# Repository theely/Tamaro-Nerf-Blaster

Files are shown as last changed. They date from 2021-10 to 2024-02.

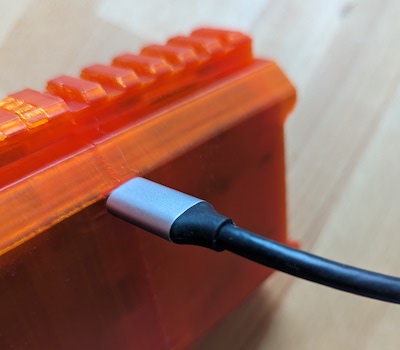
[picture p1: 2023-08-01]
docs/assets/img/tamaro-usbc-connected.jpg

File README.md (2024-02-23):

# An open-source 3D printable Nerf Rival compatible Blaster

PXL_20230726_122825097 (2)

## Mounting Instructions
Full assembly mounting instructions:
https://medium.com/@EliaPalme/tamaro-nerf-blaster-75f032bfdf08

## Part Sourcing
For convenience we offer pre-sourced hardware and electronics kit:
https://www.etsy.com/shop/TamaroBlaster

## Tamaro Blaster Configurator
The configurator allows you to fine-tune the parameters of your blaster. 
https://theely.github.io/Tamaro-Nerf-Blaster/

## Design Principles

The Tamaro blaster is inspired by the FDL3 and the OOD Jupiter blasters.
It has been designed with the following principles in mind:

### Simplicity and Elegance
Tamaro design focuses on minimalism and aesthetics, increases reliability and does not compromise on functionality.

### Small footprint
Tamaro total weight is 500g and dimensions are 245mm*158mm*48mm.

### Easy to print
Tamaro is made of 15 3D printed pieces with limited support required.

### Easy to source hardware
Tamaro only requires few M3 screws. The electronics is broadly available.

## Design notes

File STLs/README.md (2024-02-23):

# Printing Instructions

**Important: Don't change the parts orientation.**    
Each STL part has already been placed with the best possible orientation to reduce need for support and to improve print quality.

## Handles
- Support: Yes (slicer default works fine)
- Bridging: Yes (reduces need for support)
- Infil: 15%-20%
- Top solid layers: 4+

## Trigger
- Support: No
- Bridging: No
- Infil: 15%

## Magwell
- STL files: v1 for legacy magazines, v2 for the latest Nerf version.
- Support: Yes (custom)  
  Only the very bottom part requires support (see screenshot).
- Bridging: Yes
- Infil: 15%
 
Slicing Example

## Barrel
- Support: No
- Bridging: No
- Infil: 15%

## Motor Plates
- Support: No
- Bridging: No
- Infil: 40%
- Top and Bottom solid layers: 5+

## Clamp Front
- Support: No
- Bridging: No
- Infil: 20%

## Clamp Back
- Support: Yes (custom)  
  No support needed in screw and nut holes (see screenshot).
- Bridging: Yes
- Infil: 20%

Slicing Example

## Shells
- Support: Yes (custom)
  Support for cureved and angled surfaces can be supressed. 
- Bridging: Yes
- Infil: 15%
- Brim: Optionally consider adding a custom brim (see screenshot, four 1 layer squares) to prevent warping.
  


## Battery Hatch
- Support: No
- Bridging: No
- Infil: 15%

## Pusher
- Support: Yes
- Bridging: Yes
- Top and Bottom solid layers: 5+
- Perimeters: 5+
- Infil: 50%

## Battery Holder (optional)
This piece is optional and only needed if you would like to power the bluster with 16650 Li-Ion batteries insted of a LiPo battery.
- Support: Yes
- Bridging: Yes
- Infil: 15%

# QA
Tracking quality assurance parts printing tests and potential improvments.

| Part | Date | Status| Notes|
|---|---|---|---|
|Handle L|14-07-2023|Not yet printed|  | 
|Handle R|14-07-2023|Not yet printed|  | 
|Shell Back|14-07-2023|Assembled no issues| Add custom brim | 
|Barrel|30-06-2023 |Assembled no issues| Fast printing helps with overhangs | 
|Magwell|30-06-2023|Assembled no issues| Not an issue but one wall is too narrow and might end up with a small hole | 
|Clamp Front|02-07-2023|Assembled no issues|  | 
|Clamp Back|02-07-2023|Assembled no issues|  | 
|Motor Plates|02-07-2023|Assembled no issues|  | 
|Trigger|02-07-2023|Assembled no issues|  | 
|Pusher|02-07-2023|Assembled no issues|  | 
|Shell Frot|05-07-2023|Assembled no issues|  |

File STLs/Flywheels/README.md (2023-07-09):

# Printing Instructions

**Important: Don't change the parts orientation.**    
Each STL part has already been placed with the best possible orientation to reduce need for support and to improve print quality.

## EMAX RS2205 Flywheel
- Support: No
- Bridging: No
- Seam position: Random
- Infil: Rectilinear (important!) 20%
- Top solid layers: 5+
- Perimeters: 5+

## T-Motor 2205 Flywheel
- Support: No
- Bridging: No
- Seam position: Random
- Infil: Rectilinear (important!) 20%
- Top solid layers: 5+
- Perimeters: 5+

# QA
Tracking quality assurance parts printing tests and potential improvments.

| Part | Date | Status| Notes|
|---|---|---|---|
|EMAX RS2205|09-07-2023 |Printing|  |

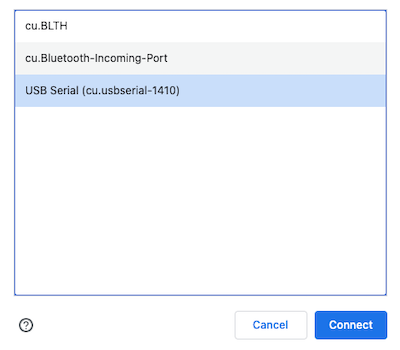
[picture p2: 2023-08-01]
docs/assets/img/select-device.jpg

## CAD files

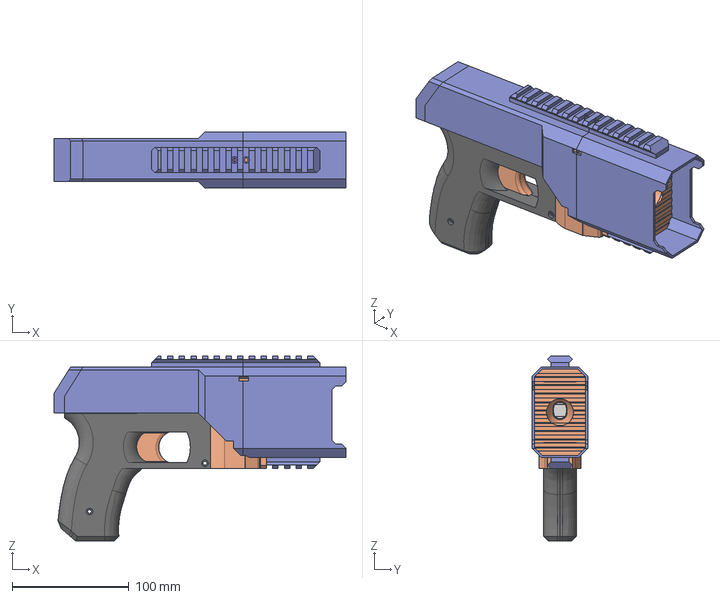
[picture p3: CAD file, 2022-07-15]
Hardware Designs Backup Exports/Blaster.stp
249.8 x 48.0 x 158.2 mm

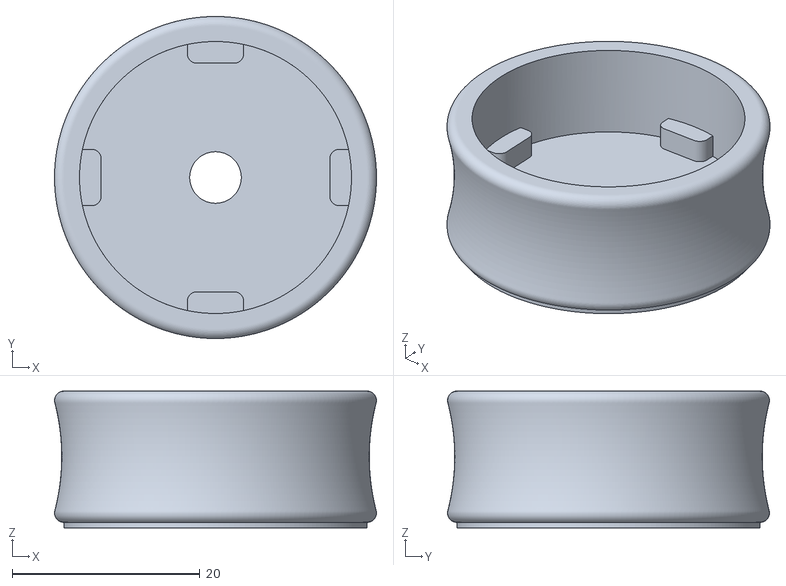
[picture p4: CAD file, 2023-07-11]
STLs/Flywheels/EMAX RS2205 (+0.5) Flywheel.stl
34.3 x 34.3 x 14.6

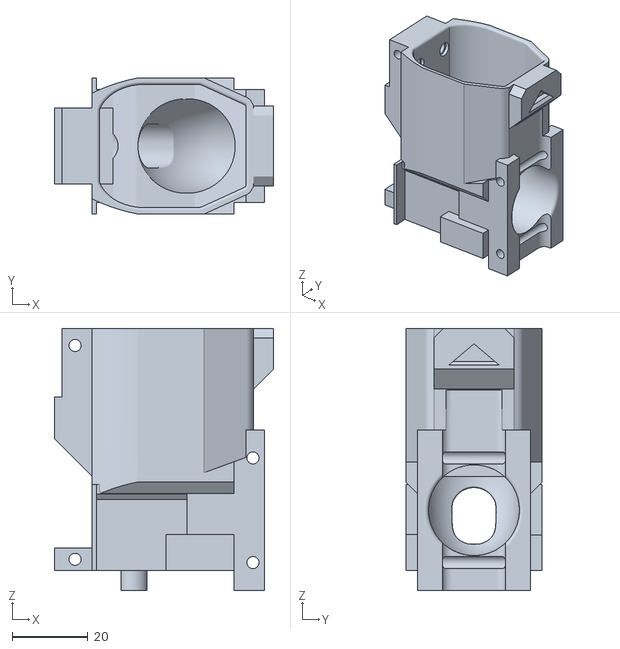
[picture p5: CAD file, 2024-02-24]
STLs/Magwell-v2.1.stl
58.1 x 36.0 x 69.4

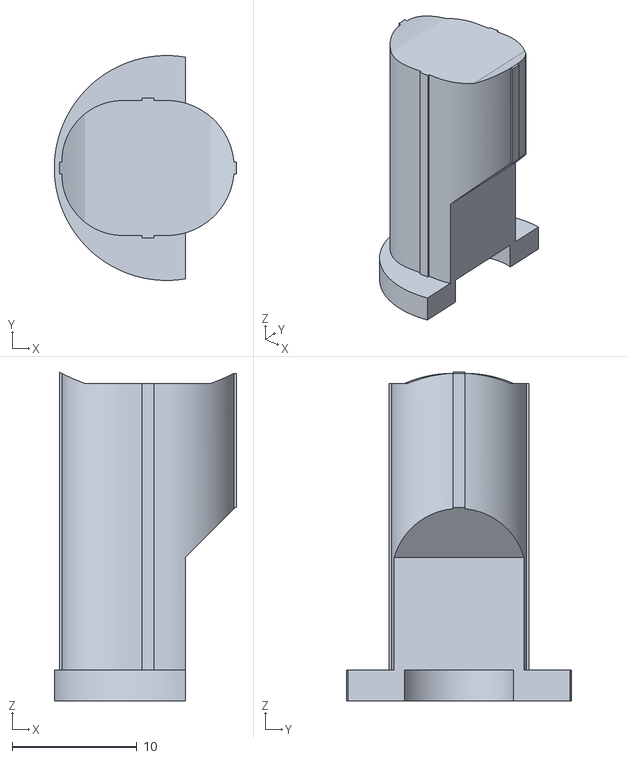
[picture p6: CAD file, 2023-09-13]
STLs/Pusher/Pusher.stl
14.6 x 18.0 x 26.3

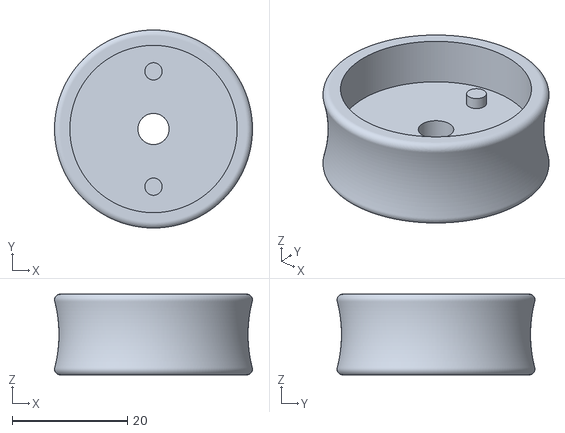
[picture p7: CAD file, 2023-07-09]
STLs/Flywheels/T-Motor 2205 (+0.4) Flywheel.stl
34.3 x 34.3 x 14.0

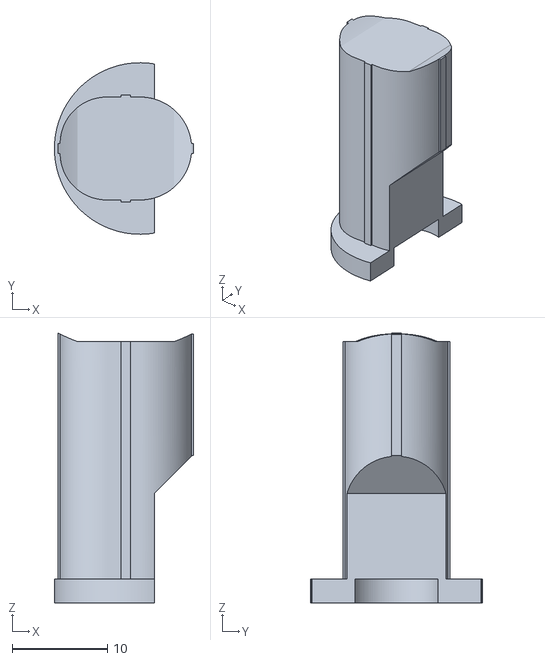
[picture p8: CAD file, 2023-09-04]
STLs/Pusher/Pusher (+2.0L).stl
14.6 x 18.0 x 28.3

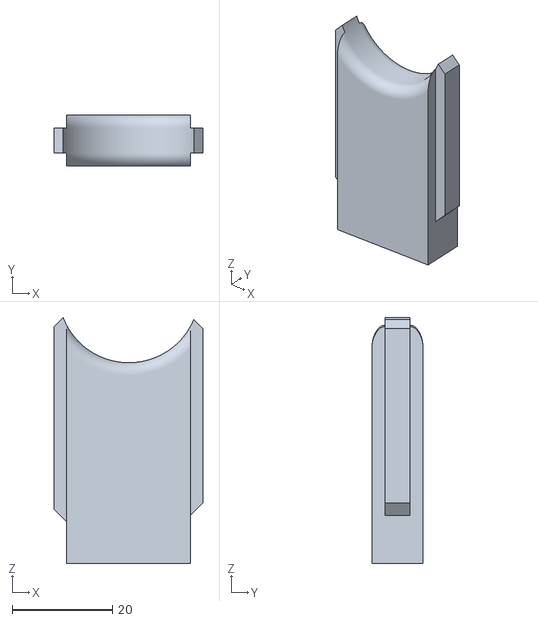
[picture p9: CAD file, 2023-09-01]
STLs/Trigger.stl
29.6 x 10.2 x 49.0

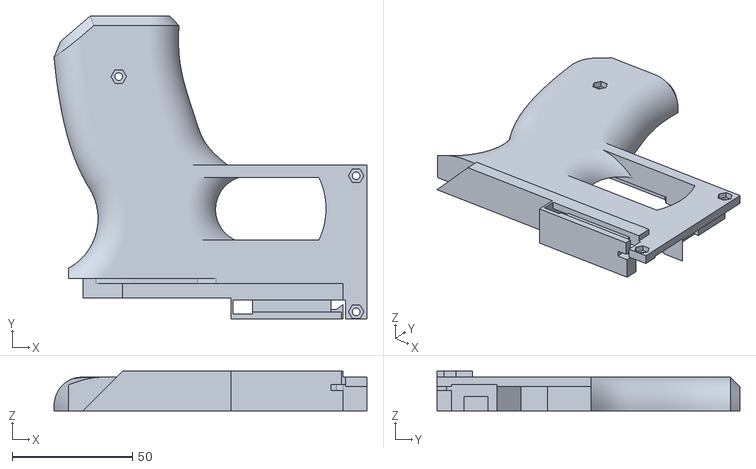
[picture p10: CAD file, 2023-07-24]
STLs/Handle L.stl
130.3 x 126.1 x 16.5

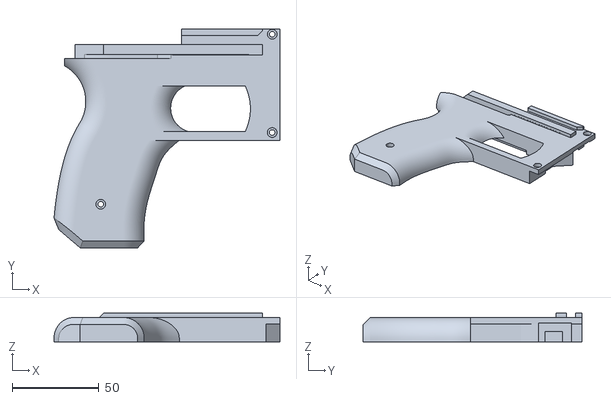
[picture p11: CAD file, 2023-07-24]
STLs/Handle R.stl
130.3 x 126.1 x 16.5

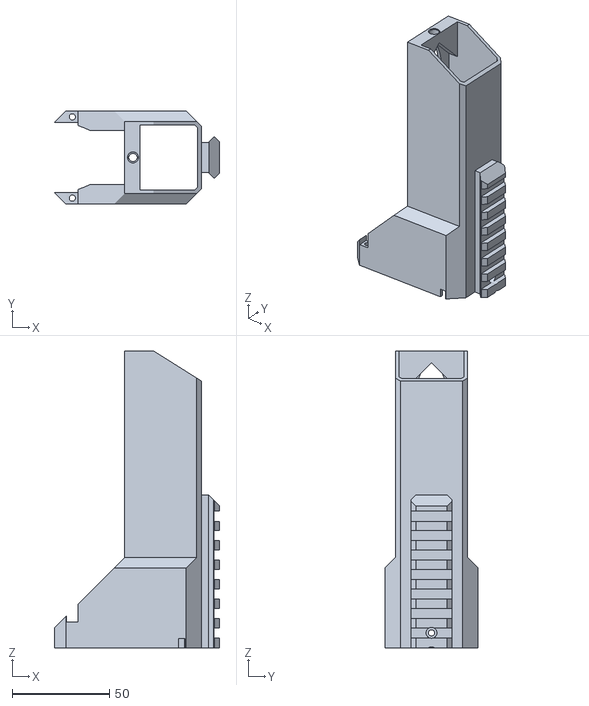
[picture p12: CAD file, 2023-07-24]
STLs/Shell Back.stl
85.0 x 48.0 x 152.8

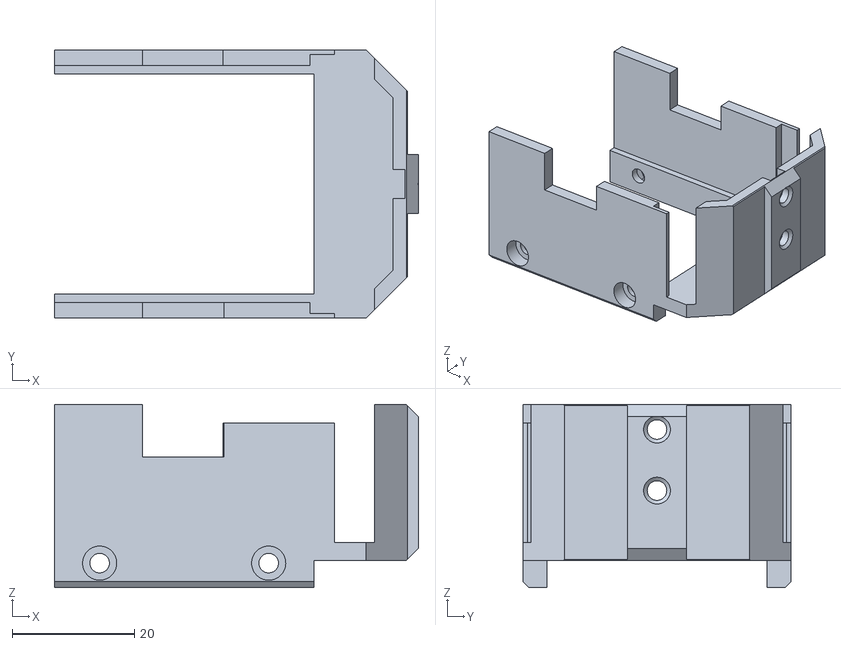
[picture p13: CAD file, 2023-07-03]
STLs/Clamp Back.stl
59.6 x 44.0 x 30.0

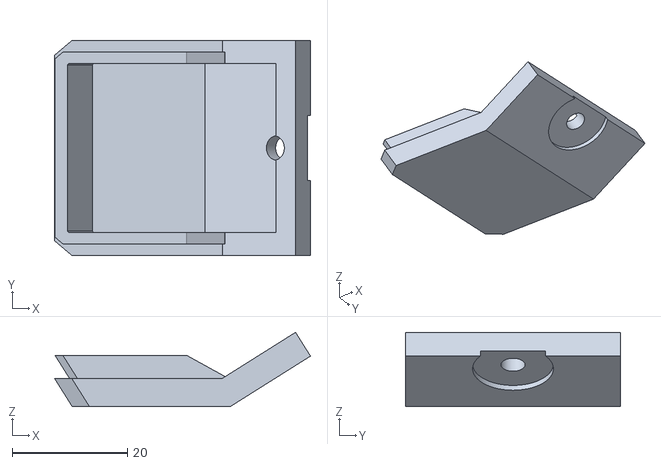
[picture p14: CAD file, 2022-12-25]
STLs/Battery Hatch.stl
44.3 x 37.2 x 12.9

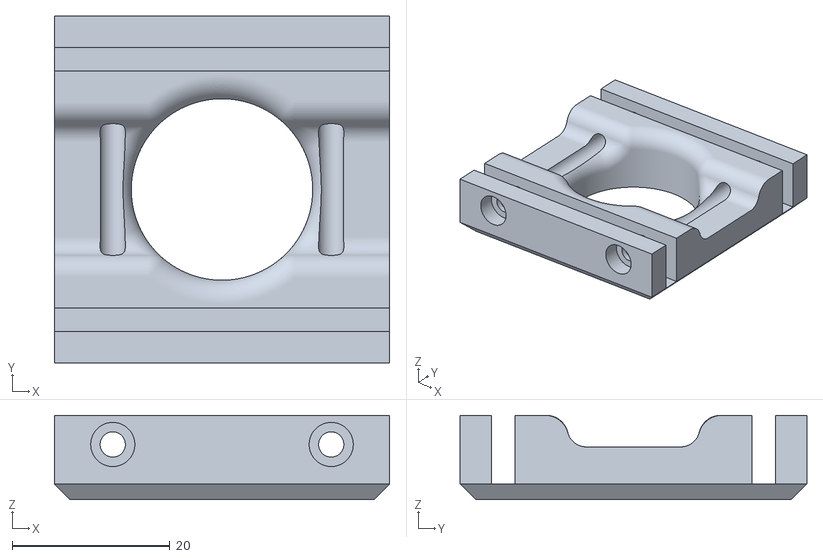
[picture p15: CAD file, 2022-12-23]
STLs/Clamp Front.stl
42.5 x 44.0 x 10.7

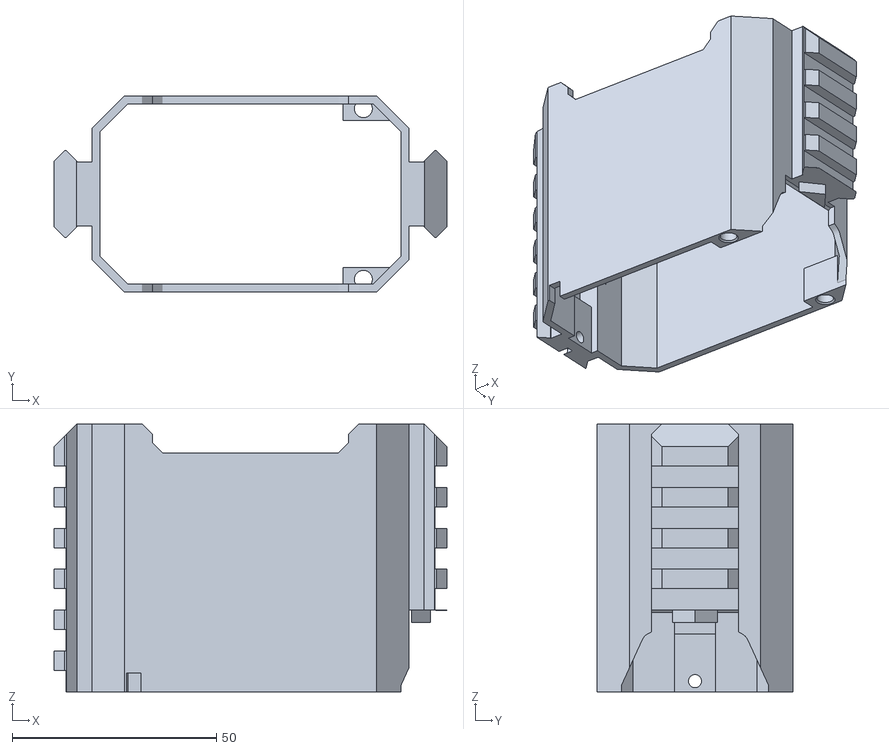
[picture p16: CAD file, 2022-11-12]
STLs/Shell Front.stl
96.2 x 48.0 x 65.5

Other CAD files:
STLs/Flywheels/EMAX RS2205 (+0.4) Flywheel.stl
STLs/Pusher/Pusher (+2.0L +0.2C).stl
STLs/Motor Plate.stl
STLs/Barrel.stl
Hardware Designs Backup Exports/Blaster+PCB.f3z
STLs/Magwell-v1.stl

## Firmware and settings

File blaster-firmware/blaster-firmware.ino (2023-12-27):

#include "DShot.h"
#include <EEPROM.h>
#include <ButtonDebounce.h>


#define SERIAL_SPEED 115200


//TODO implment BlHeli passthrough: https://github.com/BrushlessPower/BlHeli-Passthrough



int solenoid = 2;
int esc1Pin = 3;
//4 unused
//5 unused
int esc2Pin = 6;
int triggerPin = 7;
int revPin = 8;
//9 unused
//10 unused
// 11 unused
// 12 unused

int LED = 13;

//pin 15 used for analog input A1


String version = "0.1";


#define CONFIGURATION_VERSION  10

struct Confing {
  int  pusher_pull_time;     //time required for the pusher to move
  int  pusher_push_time;     //time required for the pusher to move
  int  esc_max_power;
  int  min_rampup_time;      //time required for the flywheel to get up to speed
  int  spin_differential;    //how much slower the bottom wheel should turn
  int  inactivity_time_out;  //After how much self shutdown
  int  warning_vbat;         //Vbat voltage to trigger warning
  int  critical_vbat;        //Vbat voltage to trigger shutdown
  int  vbat_scale;           //Used to calibrate vbat measurment
  int  config_version;      //IMPORTANT: increment config version for every change of this struct
};


Confing configuration = {
  110,         //pusher_pull_time -- min: 65 (tested)
  90,          //pusher_push_time -- min: 55 (tested)
  1500,        //esc_max_power
  140,         //min_rampup_time
  150,         //spin_differential
  30,          //inactivity_time_out
  10,          //warning_vbat
  9,           //critical_vbat
  12,          //vbat_scale
  CONFIGURATION_VERSION
};

struct ConfigParam {
  String  name;
  int     default_value;
  int     max_value;
  int     min_value;
  int*    value;
};

ConfigParam config_params[9] = {
  ConfigParam{"pusher_pull_time",110,500,10,&configuration.pusher_pull_time},
  ConfigParam{"pusher_push_time",90,500,10,&configuration.pusher_push_time},
  ConfigParam{"esc_max_power",1500,2047,200,&configuration.esc_max_power},
  ConfigParam{"min_rampup_time",140,500,0,&configuration.min_rampup_time},
  ConfigParam{"spin_differential",150,300,0,&configuration.spin_differential},
  ConfigParam{"inactivity_time_out",30,60,0,&configuration.inactivity_time_out},
  ConfigParam{"warning_vbat",10,14,0,&configuration.warning_vbat},
  ConfigParam{"critical_vbat",9,14,0,&configuration.critical_vbat},
  ConfigParam{"vbat_scale",12,100,1,&configuration.vbat_scale},
};



enum states {Idle, Rampup, Ready, Fire, Hold, Click, Command};
const char* statesNames[] = {"Idle", "Rampup", "Ready", "Fire", "Hold", "Click", "Command"};

enum fireRates {Single, Auto, Burst};

enum states state = Idle;
enum states previous_state = Idle;
enum fireRates fireRate = Single;

int burstCount = 0;

String serial_command;

DShot ESC1(DShot::Mode::DSHOT300INV);
DShot ESC2(DShot::Mode::DSHOT300INV);

ButtonDebounce revButton(revPin, 40);
ButtonDebounce triggerButton(triggerPin, 40);


#if defined(__AVR_ATmega328P__)
  int long_beep=130;
  int short_beep=110;
#endif
#if defined(ARDUINO_ARCH_MEGAAVR)
  int long_beep=260;
  int short_beep=240;
#endif

unsigned long timer_rampup = 0;
unsigned long vabt_warning_timer = millis();

unsigned  int click_count=0;
unsigned long click_timeout = 500;
unsigned long inter_click_timer = 0;
unsigned long inter_click_timeout = 1000;

void setup() {

  pinMode(solenoid, OUTPUT);
  digitalWrite(solenoid, LOW);
  pinMode(LED, OUTPUT);
  digitalWrite(LED, LOW);

  Serial.begin(SERIAL_SPEED,SERIAL_8N1);


  ESC1.attach(esc1Pin);
  ESC2.attach(esc2Pin);
  ESC1.setThrottle(0);
  ESC2.setThrottle(0);
  setESC1speed(0);
  setESC2speed(0);

  analogReference(DEFAULT);

  Confing configuration_check;
  EEPROM.get( 0, configuration_check );
  if(configuration_check.config_version !=  configuration.config_version){
     //Config structure has changed reset config.
     Serial.println("Config structure mismatch detected");
     EEPROM.put(0, configuration);
     Serial.println("Re-setted configuration");
  }else{
    EEPROM.get( 0, configuration);
  }


  //initialize LiPo voltage
  getAvgLiPoVoltage();
}

void loop() {


  controlESCs();

  if (Serial.available()) {
    serial_command = Serial.readStringUntil('\n');
    char* token = strtok(serial_command.c_str(), "= ,\r\n");

    bool set_value = false;
    String variable_name;
    String variable_value;
    while (token != NULL) {

      if(strcmp(token, "version") == 0){
          Serial.println("Tamaro Blaster");
          Serial.print("version:");
          Serial.println(version);
      }

      if(strcmp(token, "vbat") == 0){
          Serial.print("vbat=");
          Serial.println(getLiPoVoltage());
      }

      if(strcmp(token, "dump") == 0){
        dump();
      }

      if (set_value && variable_name != NULL && variable_value == NULL) {
        variable_value = token;
      }
      if (set_value && variable_name == NULL) {
        variable_name = token;
      }
      if (strcmp(token, "set") == 0) {
        set_value = true;
      }
      token = strtok(NULL, "= ,\r\n");
    }

    if (set_value && variable_name != NULL && variable_value != NULL) {
      setSerialParam(variable_name, variable_value.toInt());
      EEPROM.put(0, configuration);
    }



  }

  state = getState();


  if(configuration.warning_vbat> 0 && getAvgLiPoVoltage() < configuration.warning_vbat){
      if((millis() - vabt_warning_timer)  > 10000){
        beep beeps[2];
        beeps[0]= {1, short_beep};
        beeps[1]= {1, short_beep};
        ESC1.sequenceBeep(beeps,2);
        vabt_warning_timer = millis();
      }
  }
  if(configuration.critical_vbat > 0 && getAvgLiPoVoltage() < configuration.critical_vbat){
    //TOODO disable blaster and allert
  }



  if (state == Rampup || state == Ready || state == Fire ) {

    digitalWrite(LED, HIGH);

    setESC1speed(configuration.esc_max_power);
    setESC2speed(max(configuration.esc_max_power-configuration.spin_differential,48));

  } else {
    digitalWrite(LED, LOW );

    setESC1speed(0);
    setESC2speed(0);
  }

  if (state == Fire ) {

    digitalWrite(solenoid, HIGH);
    delay(configuration.pusher_pull_time);
    digitalWrite(solenoid, LOW);
    delay(configuration.pusher_push_time);
  }
  if (state == Command) {

    click_count=0;
    ESC1.setThrottle(0);
    ESC2.setThrottle(0);
    delay(300);

    if (fireRate == Single) {
      fireRate = Burst;
      //   short - 3
      beep beeps[4];
      beeps[0]= {4, long_beep};
      beeps[1]= {1, short_beep};
      beeps[2]= {1, short_beep};
      beeps[3]= {1, short_beep};
      ESC1.sequenceBeep(beeps,4);
    } else if (fireRate == Burst) {
      fireRate = Auto;
      beep beeps[4];
      beeps[0]= {4, long_beep};
      beeps[1]= {1, short_beep};
      beeps[2]= {2, short_beep};
      beeps[3]= {3, short_beep};
      ESC1.sequenceBeep(beeps,4);
    } else {
      fireRate = Single;
       //   short - short
      beep beeps[2];
      beeps[0]= {4, long_beep};
      beeps[1]= {1, short_beep};
      ESC1.sequenceBeep(beeps,2);
    }
    delay(300);
  }

  //keep this statement at end of the loop
  if (previous_state != state) {
    //Serial.println(statesNames[state]);
    previous_state = state;
  }

}

enum states getState() {


    revButton.update();
    triggerButton.update();

    int revValue = !revButton.state();
    int triggerValue = !triggerButton.state();




  switch (state) {


    case Idle:
      if (revValue == HIGH) {
        timer_rampup = millis();
        return Rampup;
      }
      if (click_count > 1) {
        return Command;
      }
      return Idle;
      break;


    case Rampup :
      if (revValue == HIGH && (millis() - timer_rampup) > configuration.min_rampup_time) {
        return Ready;
      }
      if (revValue == HIGH) {
        return Rampup;
      }
      if (revValue == LOW && (millis() - timer_rampup) < click_timeout) {
        if((millis() - inter_click_timer) > inter_click_timeout){
          click_count=1;
        }else{
          click_count++;
        }
        inter_click_timer=millis();
        return Idle;
      }
      break;

    case Ready :
      if (triggerValue == HIGH) {
        burstCount = 1;
        return Fire;
      }
      if (revValue == HIGH && triggerValue == LOW) {
        return Ready;
      }
      break;

    case Fire:
      if (fireRate == Auto && triggerValue == HIGH) {
        return Fire;
      }
      if (fireRate == Burst && triggerValue == HIGH && burstCount < 3) {
        burstCount++;
        return Fire;
      }
      if (triggerValue == LOW) {
        return Idle;
      }
      return Hold;

    case Hold:
      if (revValue == LOW) {
        return Idle;
      }
      return Hold;


    default : break;
  }

  return Idle;
}


int esc1ActualSpeed = 0;
int esc2ActualSpeed = 0;
int esc1TargetSpeed = 0;
int esc2TargetSpeed = 0;


long timer_break_esc1 = 0;
long timer_break_esc2 = 0;

void setESC1speed(int speed){
   esc1TargetSpeed = speed;
}

void setESC2speed(int speed){
    esc2TargetSpeed = speed;
}

void controlESCs(){


  //Gradual speed decrease is required to avoid voltage spikes that would accidentally trigger the solenoid

  if(esc1ActualSpeed<esc1TargetSpeed){
    esc1ActualSpeed = esc1TargetSpeed;
    ESC1.setThrottle(esc1ActualSpeed);
  }else if(esc1ActualSpeed>esc1TargetSpeed && (millis() - timer_break_esc1 > 20)){
      timer_break_esc1 = millis();
      esc1ActualSpeed-=150;
      if(esc1ActualSpeed < esc1TargetSpeed){
        esc1ActualSpeed = esc1TargetSpeed;
      }
      ESC1.setThrottle(esc1ActualSpeed);
  }

  if(esc2ActualSpeed<esc2TargetSpeed){
    esc2ActualSpeed = esc2TargetSpeed;
    ESC2.setThrottle(esc2ActualSpeed);
  }else if(esc2ActualSpeed>esc2TargetSpeed && (millis() - timer_break_esc2 > 20)){
    timer_break_esc2 = millis();
    esc2ActualSpeed-=150;
    if(esc2ActualSpeed < esc2TargetSpeed){
      esc2ActualSpeed = esc2TargetSpeed;
    }
    ESC2.setThrottle(esc2ActualSpeed);
  }



}


void setSerialParam(String param, int value){

  for(int i=0;i<sizeof config_params/sizeof(struct ConfigParam);i++){
    if(param == config_params[i].name){

      if(value < config_params[i].min_value){
        Serial.print("Minimum value for ");
        Serial.print(param);
        Serial.print(" is ");
        Serial.println(config_params[i].min_value);
        return;
      }
      if(value > config_params[i].max_value){
        Serial.print("Maximum value for ");
        Serial.print(param);
        Serial.print(" is ");
        Serial.println(config_params[i].max_value);
        return;
      }

      *config_params[i].value=value;
      EEPROM.put(0, configuration);

      Serial.print(param);
      Serial.print(" set to ");
      Serial.println(value);

      return;
    }
  }
}


void dump(){

  for(int i=0;i<sizeof config_params/sizeof(struct ConfigParam);i++){
     Serial.print(config_params[i].name);
     Serial.print("=");
     Serial.println(*config_params[i].value);
  }
}



float getLiPoVoltage(){

  //https://www.arduino.cc/reference/en/language/functions/analog-io/analogread/
  //https://skillbank.co.uk/arduino/measure.htm


  float value = analogRead(A1);
  float voltage = (value + 0.5) * 5.0 / 1023.0 *   ((float) configuration.vbat_scale); //adj_multiplier
  //Calibration formula: current_scale * (actual_vbat / measured_vbat) = new_scale

  return voltage;
  }


float vbat_avg = 0;

float getAvgLiPoVoltage(){

  float voltage = getLiPoVoltage();

  //To deal with battery sag voltage is measured as exponential moving average.
  if(vbat_avg == 0){
    vbat_avg = voltage;
  }else{
    static float alpha = 0.001; //must be between 0 and 1, the higher the faster it converges
    vbat_avg = (alpha * voltage) + (1.0 - alpha) * vbat_avg;
  }

  return vbat_avg;
  }

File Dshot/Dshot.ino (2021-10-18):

#include "DShot.h"

DShot esc1(DShot::Mode::DSHOT300INV);
DShot esc2(DShot::Mode::DSHOT300INV);

uint16_t throttle = 48;
uint16_t target = 0;

void setup() {
  // put your setup code here, to run once:
 Serial.begin(115200); 
 esc1.attach(3);
 esc1.setThrottle(throttle);
 
 esc2.attach(6);
 esc2.setThrottle(throttle);
}

int count=0;

void loop() {


 if (Serial.available()>0){
    int serial_int = Serial.parseInt();
    if(serial_int!=0){
      if(serial_int >0 && serial_int <= 2047){
        throttle = serial_int;
      }
      if(serial_int==6000){

        if(count==0){
          // short - long
          beep beeps[2];
          beeps[0]= {5, 220};
          beeps[1]= {1, 260};
          esc1.sequenceBeep(beeps,2);
        }else if(count==1){
           //   short - short
          beep beeps[2];
          beeps[0]= {2, 220};
          beeps[1]= {1, 260};
          esc1.sequenceBeep(beeps,2);
        }else{
            //   short - 3
          beep beeps[4];
          beeps[0]= {3, 220};
          beeps[1]= {3, 220};
          beeps[2]= {3, 220};
          beeps[3]= {1, 260};
          esc1.sequenceBeep(beeps,4);
        }
        count++;
        count=count%3;
        
        return;
      }
      if(serial_int==5000){
        throttle = 0;
      }
      Serial.print("Command: ");
      Serial.println(throttle);
      esc1.setThrottle(throttle);
      esc2.setThrottle(throttle);
    }
  }
  
    delay(10);
}

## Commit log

2021-10-09 Added dshot experimentation
    Re-implemented dshot assembler
2021-10-09 functional inverted dshot 300
    [DShot.cpp, DShot.h, Dshot.ino]
2021-10-10 fix to enable Beep command
    [DShot.cpp, DShot.h, Dshot.ino]
2021-10-18 fixed issue with config structure changes and cold sart
    [DShot.cpp, DShot.h, Dshot.ino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]
2021-11-10 removed filter to work with Arduino clones
2021-12-07 Fixed dShot for ATmega328P
    [DShot.cpp]
2022-07-05 button Debounce + state flow fixes
    [blaster-firmware.ino]
2022-07-08 added test code to use different timers
2022-07-08 Fixed Arduino Every Dshot bug
    [DShot.cpp]
2022-07-08 Improved compatibility cross boards
2022-07-09 improved esc initialization
2022-07-15 Uploading Fusion 360 exports
    [Blaster+PCB.f3z, Blaster.stp]
2022-08-27 Simplified Flow without double click
2022-11-11 Beep Fix and Power Ramp-down
    [blaster-firmware.ino]
2022-11-12 added STL files
    [Barrel.stl, Battery Hatch.stl, Battery Holder.stl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]
2022-11-12 added print read me
2022-11-18 Added pusher, fixed Handle
    [Handle L.stl, Pusher.stl]
2022-12-12 Fixed Clamp and Pusher
    [Clamp Back.stl, Pusher.stl]
2022-12-18 fixed cable routing
    [Handle L.stl]
2022-12-23 Added chamfer to make shell insertion easier
    [Battery Hatch.stl, Clamp Back.stl, Clamp Front.stl]
2022-12-23 Deprecated support for LiOn batteries
    [Battery Holder.stl]
2022-12-25 smaller hatch
    [Battery Hatch.stl]
2022-12-29 allowing to disable battery warning
2022-12-29 update angular material to v13
2022-12-29 update angular material 10 v14
2022-12-29 updated to angular material v15
2022-12-29 Improved voltage reading
2022-12-29 added direct and avaraged LiPo voltage read
2023-07-03 Fixed orientation
    [Clamp Back.stl]
2023-07-03 Removed duplicate Motor Plate
    [Motor Plate.stl]
2023-07-07 Simpler Pusher with increased tolerances
    [Pusher.stl]
2023-07-07 Pusher with Ring
    [Pusher.stl]
2023-07-07 added more tolerance to pusher
    [Pusher.stl]
2023-07-07 Removed spacing for lithium batteries
    [Shell Back.stl]
2023-07-07 Fixed missing spacer
    [Pusher.stl]
2023-07-07 added spacing for additional friction
    [Pusher.stl]
2023-07-14 Added 0.4 extra tolerance
    [Shell Back.stl]
2023-07-14 removed the un necessary lithium battery insert
    [Handle L.stl, Handle R.stl]
2023-07-14 fixed missing insert
    [Handle L.stl]
2023-07-15 fixed missing insert for buttons
    [Shell Back.stl]
2023-07-24 Removed support for buttons
    Semplified design
    [Handle L.stl, Handle R.stl, Shell Back.stl]
2023-08-26 Added extra tolerances for magazine
    [Magwell.stl]
2023-09-01 Improved Tollerances
    [Trigger.stl]
2023-09-01 Improved spring tension
    [Trigger.stl]
2023-09-04 Added pusher with smaller hole
    [Pusher (+0.2).stl]
2023-09-13 Added more variations with better naming
    [Pusher (+2.0L +0.2C).stl, Pusher (+2.0L).stl, Pusher.stl]
2023-12-26 updated esc break speed
2023-12-27 increased default max esc speed to 1500
2024-02-10 Delete STLs/Button.stl (#3)
    PCB design with buttons has been deprecated.
    [Button.stl]
2024-02-10 Update README.md
    Buttons have been deprecated
2024-02-23 Added compatibility for latest version of Nerf Rival magazine
    [Magwell-v2.stl]
2024-02-24 Updated dents holes
    [Magwell-v2.1.stl]
